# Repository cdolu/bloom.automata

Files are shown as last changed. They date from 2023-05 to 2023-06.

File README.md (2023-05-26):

# A Study On The Design And Manufacturing Of Mechanical Sculptures: The Blooming Flowers Automata

Hello!

This study provides the documentation and methodology necessary for designing, testing, and manufacturing advanced automata using widely available materials while utilizing design engineering principles. The automata have no electrical pieces such as motors or sensors, focusing on simple machines, specifically gears and levers to automate the mechanical sculpture. 

A modified Engineering Design Process (EDP) is created to cater to high school students and utilize CAD environments for high-fidelity prototyping, as well as compensate for the problems in estimating engineering quantities without experience. It explored the implementation of constructivist approach in K-12 level and quick prototyping education. On that branch, the curricula for gear theory and fundamental law/s are adapted to the high school level for users with rudimentary to no grasp of mechanics as a proper understanding of gear theory is necessary. 

A laser cutter is used for the quick prototyping of the automata, however, the design can be manufactured by hand with plywood or MDF and easily accessible tools such as hand saws and wood files. Making bevel gears is challenging and timely without a machine like a CNC because of their conical-shaped teeth. To compensate for this, cage and peg gears are used. Additionally, the gears are developed for the sculpture using gear theory to achieve peg gear trains with nonparallel axes of rotation. The real-life constraints of mechanical design engineering are dealt with by utilizing the mod. EDP and gear theory in the following study.

Every step and method used in the study is opensource and available on this repository. For more of my projects, some of which are in a similar vein, you can visit my website linked on my profile. I take credit only for my own work, third-party contributors are referenced and not subject this projects' license! 



This work is licensed under a Creative Commons Attribution-NonCommercial-ShareAlike 4.0 International License.

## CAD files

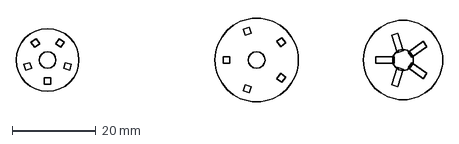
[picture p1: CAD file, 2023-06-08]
flower dxf/yeni tabak no center constraint.dxf
102.0 x 20.0 mm

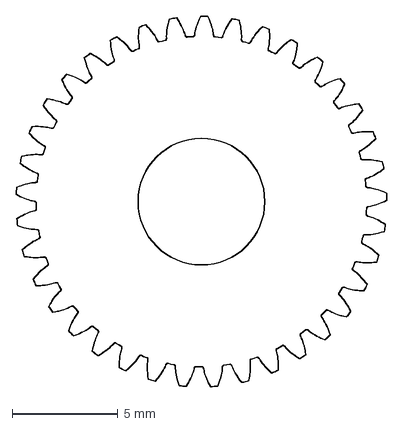
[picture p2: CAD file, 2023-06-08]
gears dxf/dişleri var olan pinion.dxf
17.5 x 17.5 mm

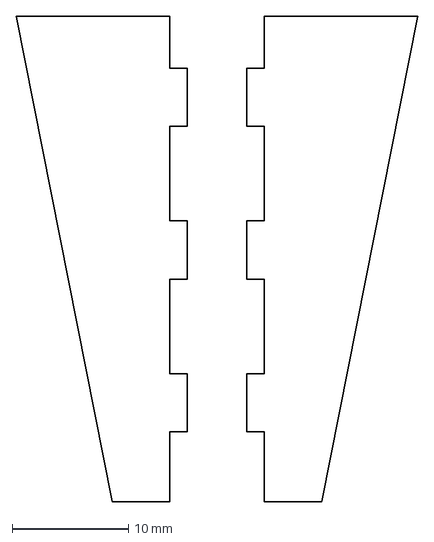
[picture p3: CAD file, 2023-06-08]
flower dxf/alt yaprak.dxf
34.5 x 41.7 mm

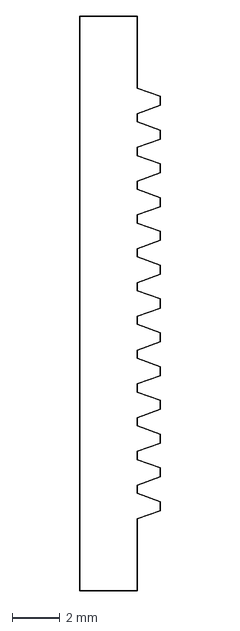
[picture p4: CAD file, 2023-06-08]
gears dxf/rack.dxf
3.36 x 24.0 mm

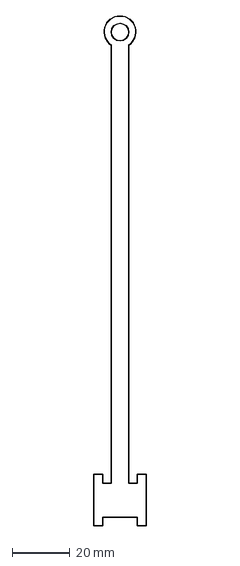
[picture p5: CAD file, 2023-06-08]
gears dxf/sup M.dxf
18.0 x 176.0 mm

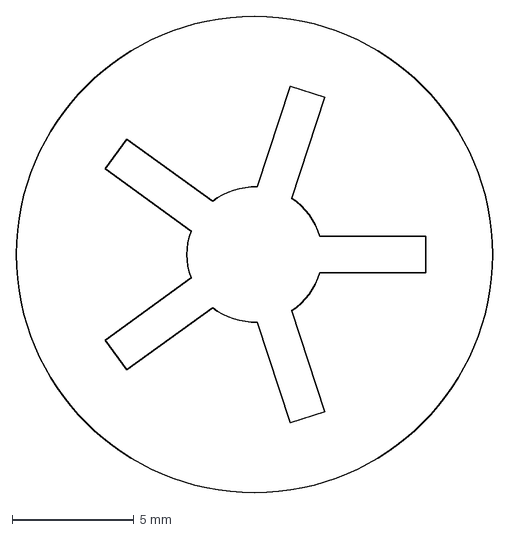
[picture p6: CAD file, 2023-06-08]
flower dxf/gereksiz olan tabak 5.55 center.dxf
19.5 x 19.5 mm

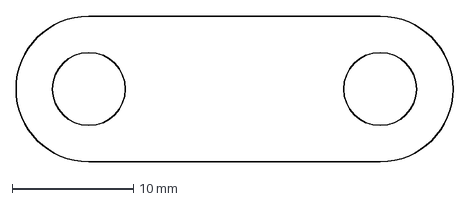
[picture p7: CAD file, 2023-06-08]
gears dxf/çalıştırma dovel.dxf
36.0 x 12.0 mm

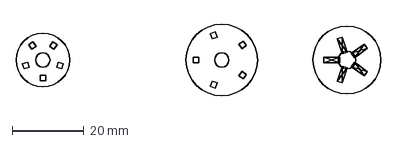
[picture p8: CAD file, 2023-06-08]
flower dxf/yeni tabaklar.dxf
102.0 x 20.0 mm

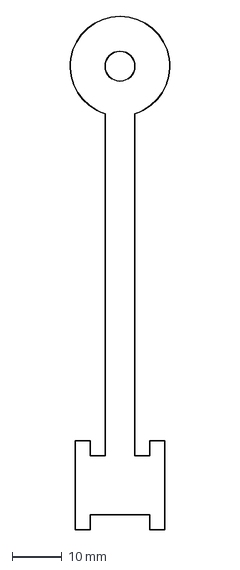
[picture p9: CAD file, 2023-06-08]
gears dxf/sup s.dxf
21.3 x 103.0 mm

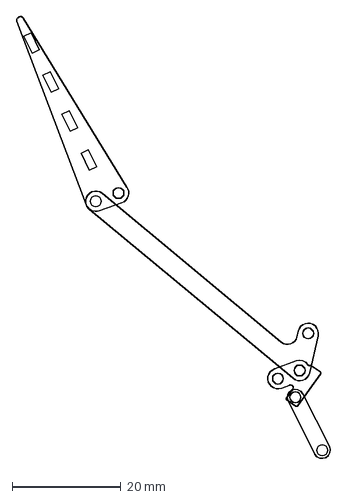
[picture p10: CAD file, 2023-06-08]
flower dxf/bir sürü.dxf
58.0 x 81.5 mm

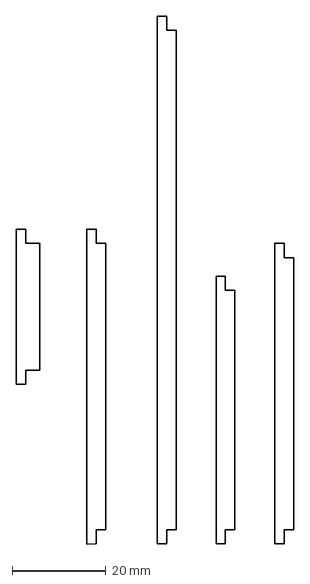
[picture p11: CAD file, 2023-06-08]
gears dxf/sütunlar.dxf
59.0 x 112.5 mm

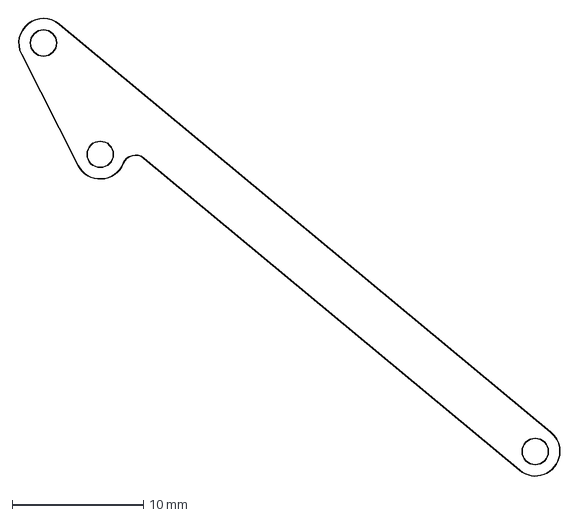
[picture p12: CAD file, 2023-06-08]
flower dxf/L v2 için.dxf
41.4 x 35.1 mm

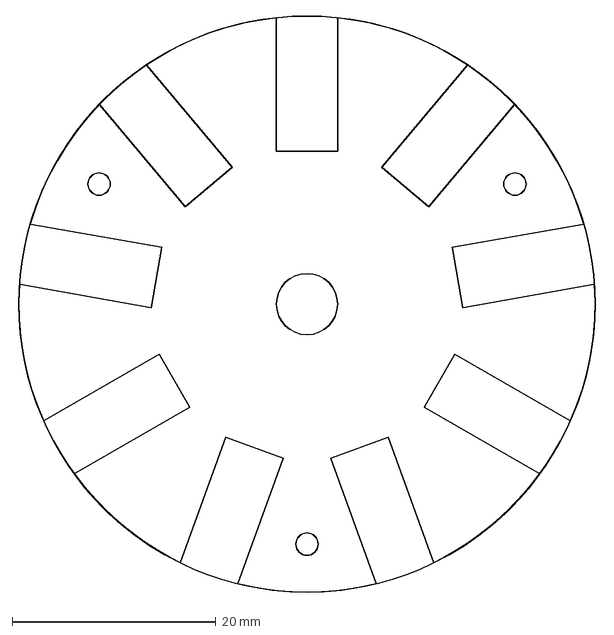
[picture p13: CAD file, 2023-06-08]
gears dxf/çıkıntı sandviç.dxf
57.0 x 56.8 mm

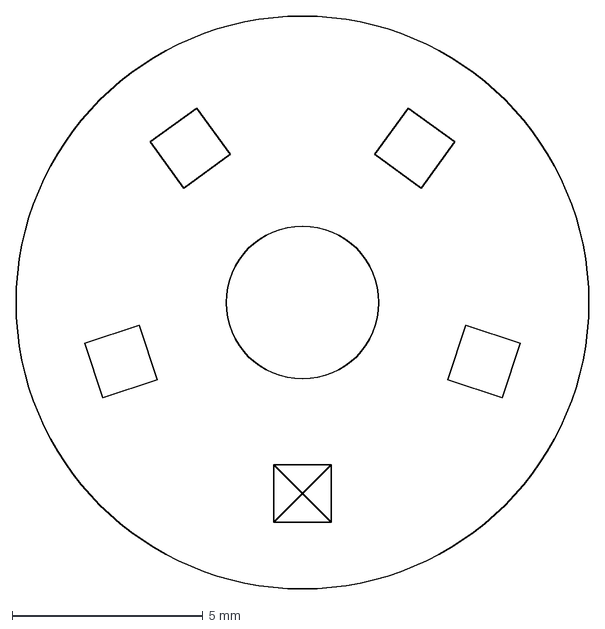
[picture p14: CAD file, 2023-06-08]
flower dxf/yuvarlak.dxf
15.0 x 15.0 mm

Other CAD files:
flower dxf/çizgi.dxf
gears dxf/satı peg.dxf
flower dxf/polygon üst yuvarlak.dxf
gears dxf/pin e bağlı recip h.dxf
flower dxf/15 mm slot and stopper circ.dxf
flower dxf/90 not L.dxf
flower dxf/alt tabak connector.dxf
flower dxf/alt tabak.dxf
flower dxf/ch.dxf
flower dxf/çiçek v1 (1).dxf
flower dxf/çizgisiz.dxf
flower dxf/donut.dxf
flower dxf/düz parça.dxf
flower dxf/l v3.dxf
flower dxf/lies.dxf
flower dxf/ray rack router.dxf
flower dxf/tabak connector.dxf
flower dxf/uzun çiçek slot 22.7 mm.dxf
flower dxf/üçgen ve connector v2.dxf
flower dxf/üst tabak.dxf
flower dxf/üst yaprak.dxf
flower dxf/yuvarlak aile.dxf
gears dxf/alt tabanlar.dxf
gears dxf/baba çarklar.dxf
gears dxf/baya stopper ve slot olan.dxf
gears dxf/düzgün alt taban.dxf
gears dxf/küçük lantern.dxf
gears dxf/pin başı.dxf
gears dxf/pinion.dxf
gears dxf/rackin yuvarlar.dxf
gears dxf/recip açılı.dxf
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

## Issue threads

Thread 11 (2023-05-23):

peg and actuator mesh fix

cdolu, 2023-05-23:
m2 screw trigonal spacing

Closed 2023-05-23.

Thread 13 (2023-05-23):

gear train fix (bc backlash)

cdolu, 2023-05-23:

Closed 2023-05-23.

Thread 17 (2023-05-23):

frame base support

cdolu, 2023-05-23:
3mm kraftplex, angled entry point, clamp with 16mm m2 screw (7 points)

cdolu, 2023-05-23:
make tangible padding(spacers)

Closed 2023-05-23.

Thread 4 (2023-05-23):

problem decomposition/ flower mechanisms sketch and elimination

cdolu, 2023-05-23:

Closed 2023-05-23.

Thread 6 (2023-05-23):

bloom mechanism prelim testing

cdolu, 2023-05-23:

cdolu, 2023-05-23:
hinges bump into each other, too much friction, slimmed down model?

Closed 2023-05-23.

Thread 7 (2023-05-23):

bloom v2

cdolu, 2023-05-23:
wire joints are too mobile, problematic to assemble, and disassembly is not possible

Closed 2023-05-23.

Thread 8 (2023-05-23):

bloom v3 (final!)

cdolu, 2023-05-23:
the top plate is a sandwich of two 1.5 krafplex, clamp pivot material with m2 screws, disassembly possible

Closed 2023-05-23.

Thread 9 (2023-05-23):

recip peg

cdolu, 2023-05-23:
check backlash, 270-degree circular segment, hor. plane rotation for flower fix dowel (upper plates)
